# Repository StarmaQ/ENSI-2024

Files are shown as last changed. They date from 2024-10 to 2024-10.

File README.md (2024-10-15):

This repository contains info that should hopefully help others building a line follower robot.

Files for the design of 5mayes are available, and the code for it too.

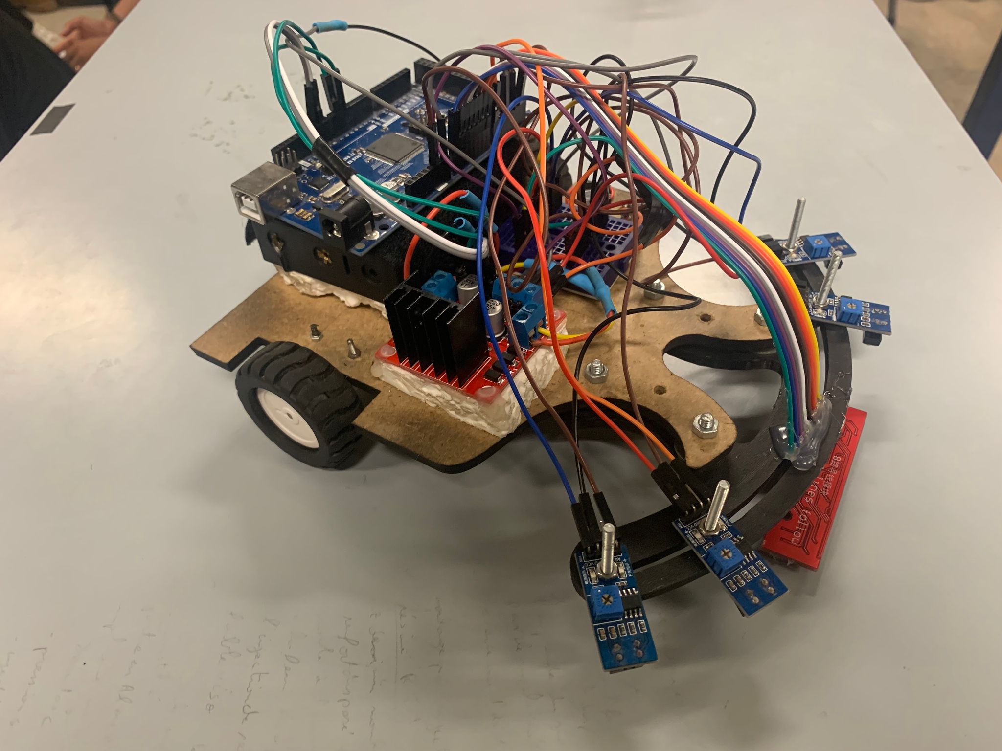
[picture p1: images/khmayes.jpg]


We used 4 IR Sensors (respectively named `farLeft`, `left`, `right` `farRight`), and the `qtr-8a`.

For generally following the line, we used the `qtr-8a`, `left` and `right` the and the PID algorithm (with $K_p = 0.06$ and $K_d = 0$).

At first our PID algorithm only relied on the `qtr_8a`, but we noticed a very good improvement when we added `left` and `right` to the error calculation, giving both very high weights compared to the middle sensors of the qtr. This made it it impossible for 5mayes to exit the line, as it strongly corrected itself if it did so.

With the PID alone we were able to traverse most of the map, but we had to flag various sections of the map, to be aware of where 5mayes was, and what the next obstacle was. 

Flagging each obstacle involved making 5mayes move, setting up a flag that involved checking what combination of `isRight()`, `isLeft()`, `isFarLeft()` and `isFarRight()` was returning true (we even relied on the values from the qtr using `digitalSensors[i]` for some flags), calling `robotStop()` when the flag was activated to debug whether the flag was correct or not, and whether it had a high chance of failure or not.

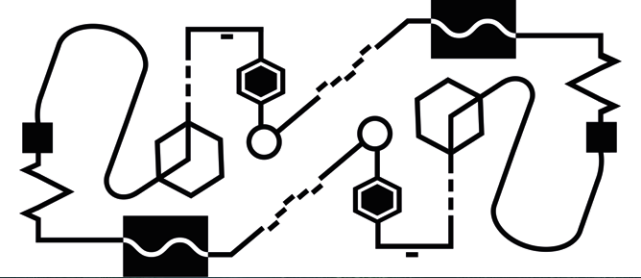
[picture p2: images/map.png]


The main thing about making a line follower robot is having consistent results no matter the conditions, and discovering what factors were at apply for it give to stable results was the difficulty of the challenge.

There were two major changes to 5mayes that were essential for us to achieve decent results, first one was hardware. We had a hard time at first with the IR sensors falling off their place, their height off the ground changing which made their values change, and as such we had to change threshhold and numbers all the time. The frontal part was original just MDF, we ended up 3D printing it making it more robust, and we made sure all the sensors were firmly fixed in place such that their heights don't change and their values would then become generally the same each time we tested.

Second most important change was adding an automatic calibrating function. We did two things here, we agreed on a good range of values that worked well with the threshholds and with the range for the error we calculated for the PID algorithm. Inside of `void setup()` we made a function to register the max and min value for each sensor, and then any value read during `void loop()` would be mapped from that min/max range to the range we want (e.g. IR sensors readings were always mapped between 0 and 700, as such our threshhold of 200 worked perfectly every time we tested).

Another addition was a formula we applied to our qtr. It was giving us really bad numbers, (600 when over white, 780 when over black), which resulted in an error that wouldn't make the PID algorithm function perfectly. Besides mapping to the range (0, 1023) which had a linear effect on the values, we had to apply a smoothing formula, that pretty much made values underneath a certain threshhold negligible, and favored higher values that were closer to 1023. This gave us perfect numbers that we were able to work with

```c
sensorValues[i] = (int)(pow((long double)sensorValues[i]/700, 12)*350);
```

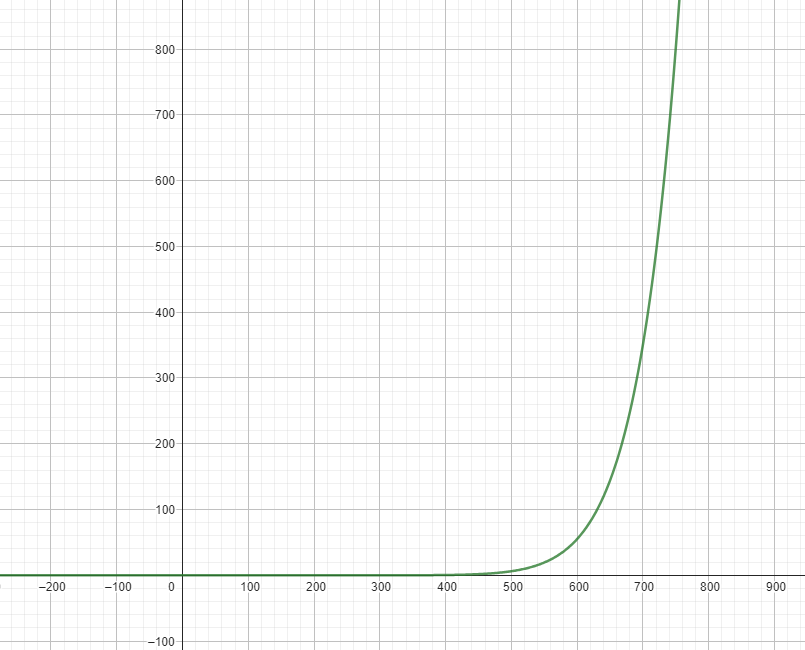
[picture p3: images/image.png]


With this, values that were under 700 were generally squashed down so that they wouldn't effect the error.

Despite our robot performing well in the map we had fil INSAT finishing most of it, it performed poorly in the ENSI, barely finishing a quarter of the map. 

Our mistake was we didn't make sure our flags were rock solid and that they worked every single time. The difficulty with line followers is having consistent results. 

Another advice is to make sure you save your latest working code! It can easily be lost, we had this issue the day of the event, and we were using code we weren't sure about, and we even made untested last minute changes that probably contributed to the 5mayes not working!

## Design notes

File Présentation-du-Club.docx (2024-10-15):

DOSSIER THECHNIQUE DU ROBOT :

KHMAYES

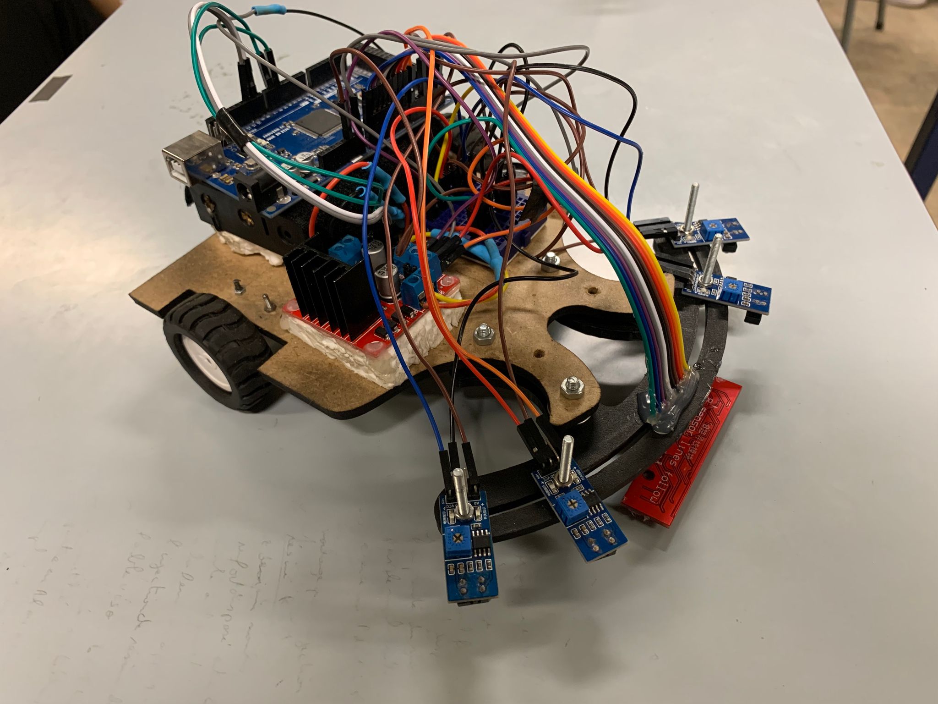
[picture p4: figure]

Présentation du Club :

Notre club est leader dans le domaine de la robotique et de l’aéronautique en Tunisie, et représente le pôle robotique et Aéronautique de l’INSAT. AEROBOTIX est une famille renfermant plus de 150 membres. Nous cherchons à rendre chaque rencontre enrichissante d’un point de vue humain et technologique. Chaque membre apporte de l’énergie aux autres, nous nous attachons à insuffler cette énergie pour innover et concrétiser nos projets qui feront objets des compétitions et des expositions nationales et internationales. Nous offrons une excellente formation pour nos membres et nous garantissons une expérience innovante, exceptionnelle et collaborative. Notre club est le club le plus performant à l’INSAT avec plus de 100 participations à des compétitions nationales, 17 participations à l’échelle internationale et remportant ainsi plusieurs prix, plus que 35 médailles et 25 trophées.

Introduction :

Le but de ce projet était de réaliser un robot capable de suivre une ligne qu’elle soit droite ou courbe. La mise en œuvre pratique était que notre robot puisse participer à une course contre le robot n˚2, réalisé par un autre groupe. La principale contrainte à laquelle nous avons dû faire face était la taille du robot, la gestion du temps et la difficulté du map. En effet, celui-ci devait respecter les dimensions mentionnées dans le cahier des charges du ROBOCUP ENSI 7.0. Pour concevoir notre robot, on nous a fourni différents éléments tels que les moteurs, les roues et la carte Arduino sur laquelle nous avons programmé le robot.

Projet

Conception sous solidworks

Realisation du cablage

Realisation du programme

Choix de la strategie

Conception du robot

Informatique

mécanique

electrique

Partie mécanique :

Pour la partie mécanique, Nous avons d’abord réfléchi sur une feuille sur laquelle nous dessinions les composants, puis on a choisi SolidWorks comme logiciel pour dimensionner notre robot en 3d. Nous avons conçu 2 bases différentes, puis nous les avons assemblés

Nous avons d’abord tracé notre base sur le bois (MDF), puis nous avons découpé celle-ci. Nous avons ensuite dû fixer un morceau de bois à angle droit sur la partie arrière il nous a juste fallu choisir les vis adaptées pour attacher les deux morceaux de bois.

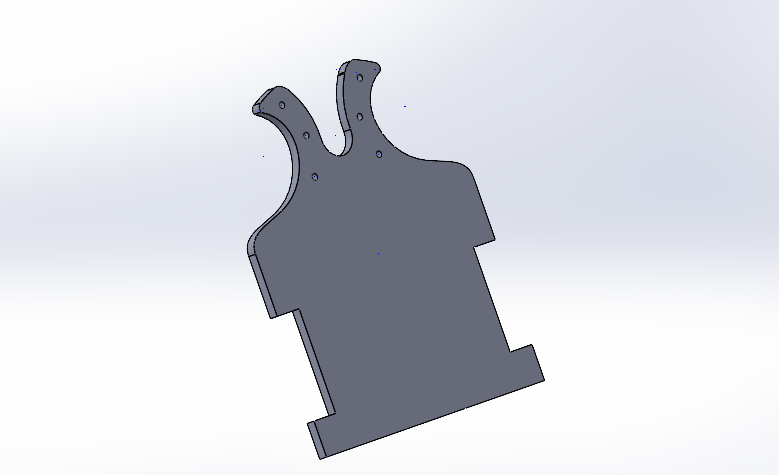
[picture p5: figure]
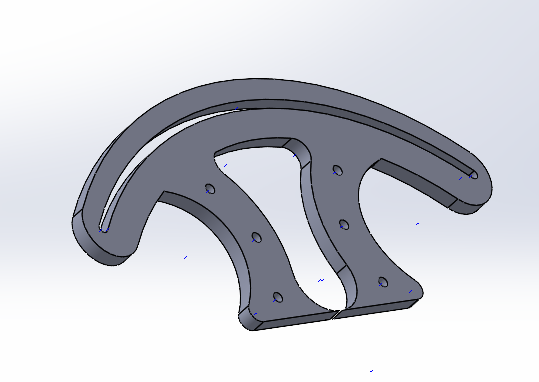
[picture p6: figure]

Composants utilisés :

QTR sensor :

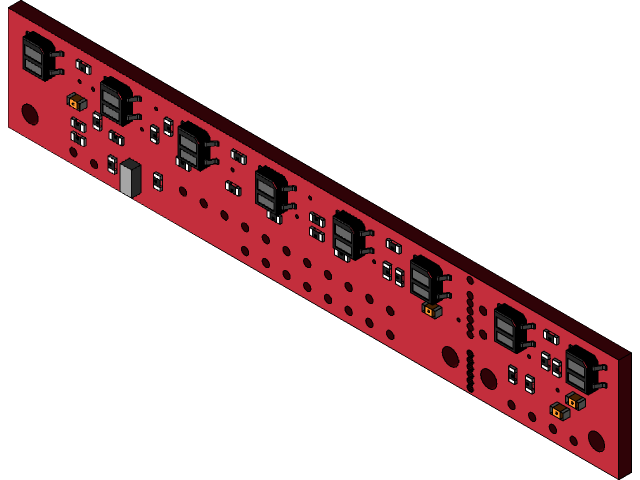
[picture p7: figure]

Moteur pololu :

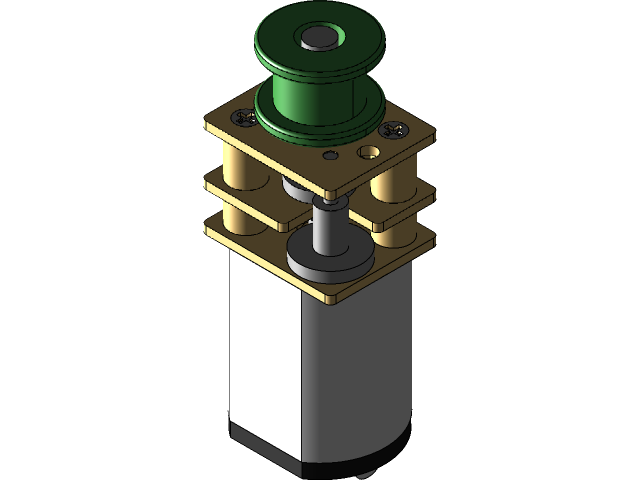
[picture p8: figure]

Carte Arduino méga :

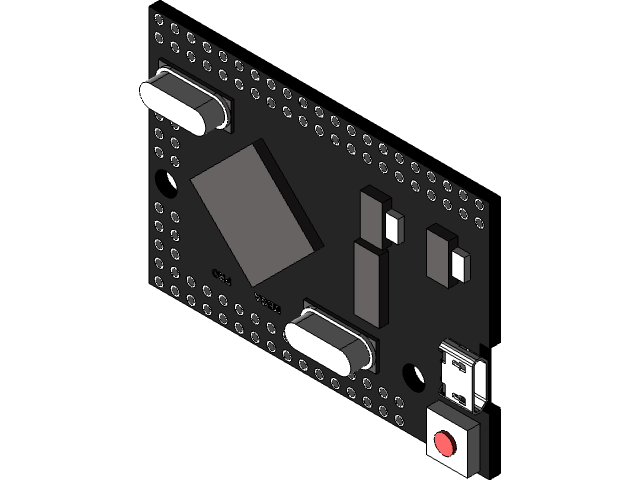
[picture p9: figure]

Capteur infrarouge :

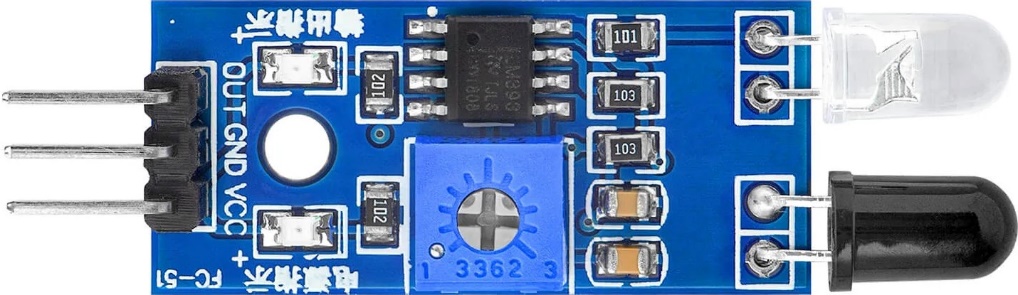
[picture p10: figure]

Carte de puissance :

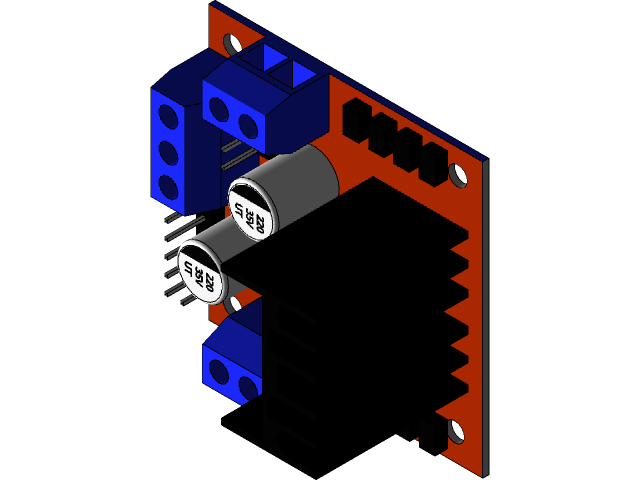
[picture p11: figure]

SCROLL

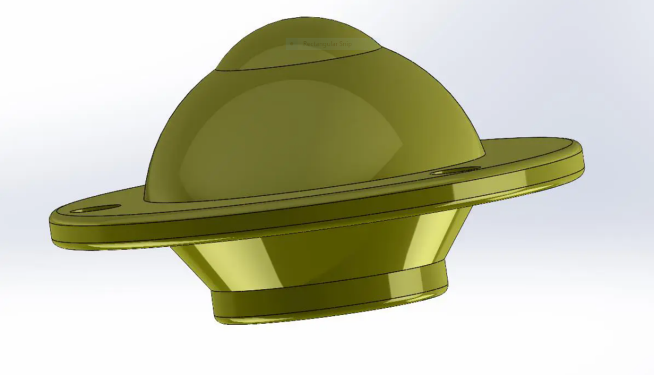
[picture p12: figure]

3 piles :

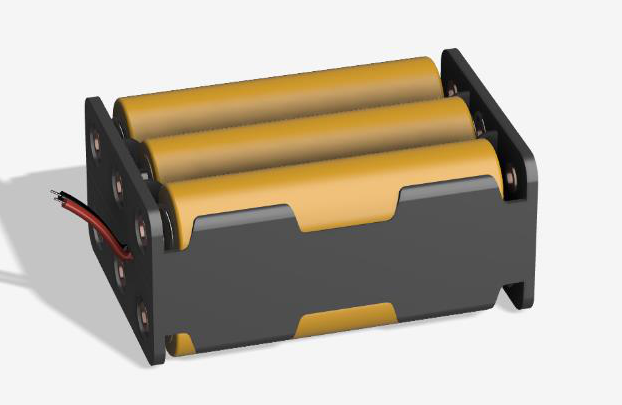
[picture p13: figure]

Conception électronique :

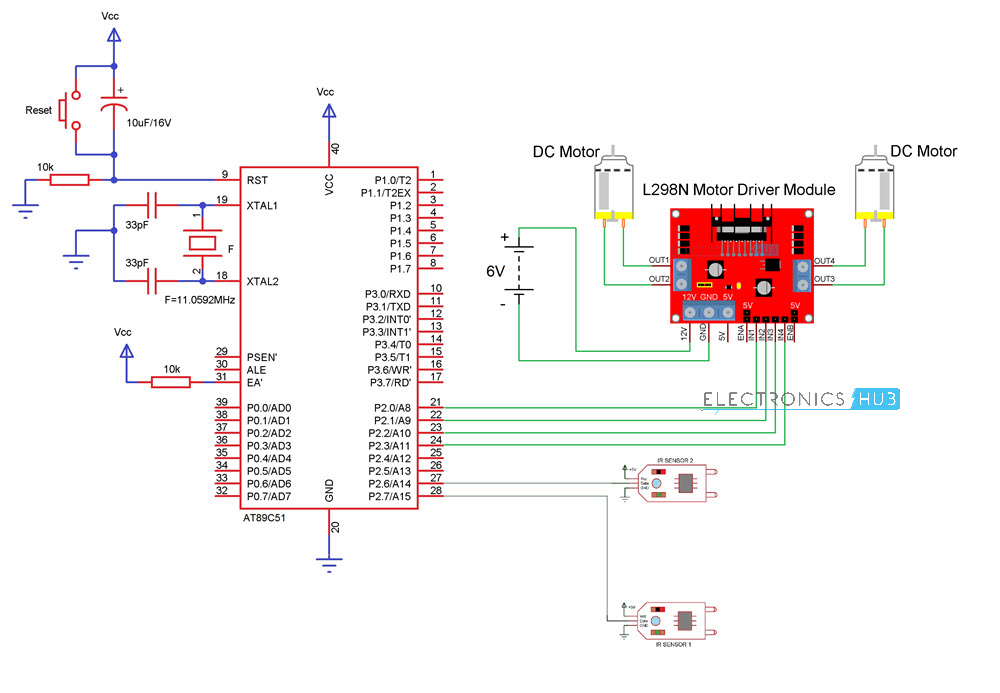
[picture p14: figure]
Line Follower Robot using Microcontroller | Engineering Projects

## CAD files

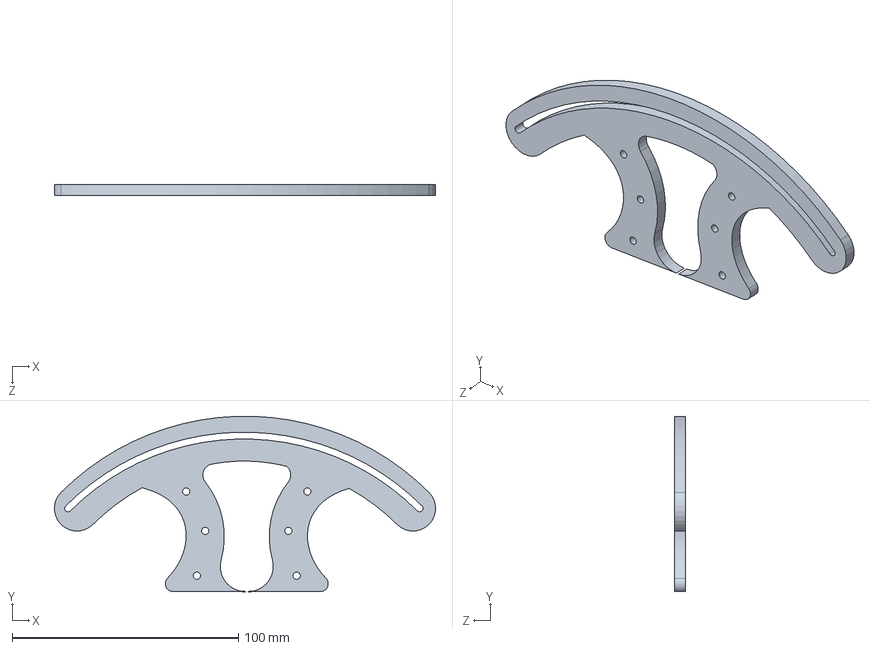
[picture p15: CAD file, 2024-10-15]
khmayess-up (1).sldprt
168.3 x 77.4 x 5.00 mm

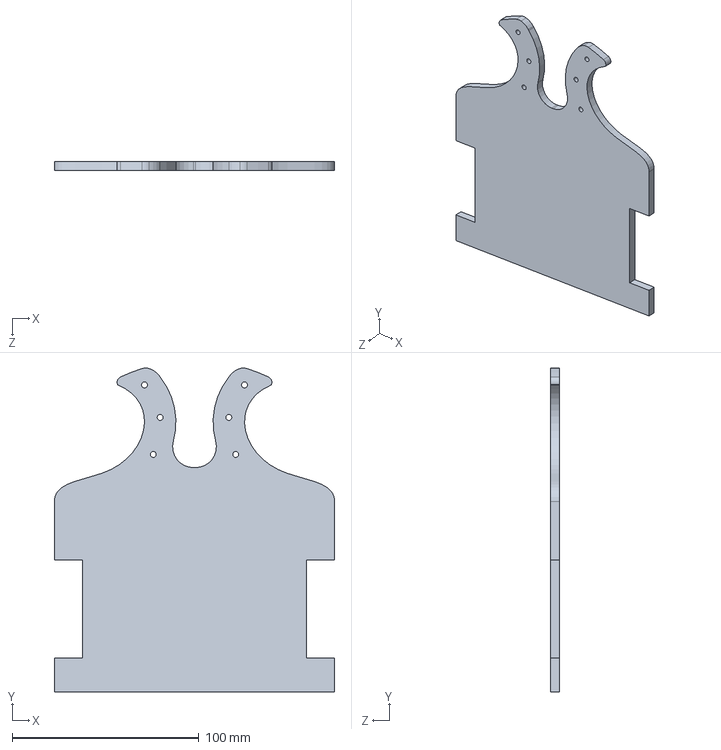
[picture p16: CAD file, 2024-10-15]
khmayessss-down (1).sldprt
150.0 x 173.4 x 5.00 mm

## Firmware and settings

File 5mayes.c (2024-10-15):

#include <QTRSensors.h>

#define m1p1 5
#define m1p2 6

#define m2p1 10
#define m2p2 9

#define rs A8
#define ls A12

#define rs2 A14
#define ls2 A11

#define NUM_SENSORS 8

float Kp = 0.06;
#define Kd 0

#define rightMaxSpeed 250
#define leftMaxSpeed 250
int cond = 0;

int inclination = 0;
int leftBaseSpeed = 120;
int rightBaseSpeed = 120;
#define threshhold 250;

QTRSensors qtra;
uint16_t sensorValues[NUM_SENSORS];
uint16_t digitalSensors[NUM_SENSORS];

#define BUFFER_SIZE 10
int rightSensorValues[BUFFER_SIZE];
int leftSensorValues[BUFFER_SIZE];
int farRightSensorValues[BUFFER_SIZE];
int farLeftSensorValues[BUFFER_SIZE];
int rightTotal = 0;
int leftTotal = 0;
int farRightTotal = 0;
int farLeftTotal = 0;
int currentIndex = 0;

bool inSecondHexagon = false;

long MAXIMUM_QTR;
long MINIMUM_QTR;


int minIRValues[4];
int maxIRValues[4];

// function to calibrate the sensors
void calibrate() {
  for (int i = 0; i < 4; i++) {
    minIRValues[i] = 1000;
    maxIRValues[i] = 0;
  }

  // for (int i = 0; i < 100; i++) {  // 100 iterations of calibration
  while (digitalRead(3) == 1) {
    int leftSensor = analogRead(ls);
    int rightSensor = analogRead(rs);
    int leftSensor2 = analogRead(ls2);
    int rightSensor2 = analogRead(rs2);

    // Update minimum values
    if (leftSensor < minIRValues[0]) minIRValues[0] = leftSensor;
    if (rightSensor < minIRValues[1]) minIRValues[1] = rightSensor;
    if (leftSensor2 < minIRValues[2]) minIRValues[2] = leftSensor2;
    if (rightSensor2 < minIRValues[3]) minIRValues[3] = rightSensor2;

    // Update maximum values
    if (leftSensor > maxIRValues[0]) maxIRValues[0] = leftSensor;
    if (rightSensor > maxIRValues[1]) maxIRValues[1] = rightSensor;
    if (leftSensor2 > maxIRValues[2]) maxIRValues[2] = leftSensor2;
    if (rightSensor2 > maxIRValues[3]) maxIRValues[3] = rightSensor2;

    // function provided by the qtra library
    qtra.calibrate();
  
    delay(10);
  }


  long sumMaximum = 0;
  long sumMinimum = 0;

  for (int i = 0; i < NUM_SENSORS; i++) {
    sumMaximum = sumMaximum + qtra.calibrationOn.maximum[i];
    sumMinimum = sumMinimum+ qtra.calibrationOn.minimum[i];
  }
  MAXIMUM_QTR=sumMaximum/(NUM_SENSORS);
  MINIMUM_QTR=sumMinimum/(NUM_SENSORS);
}

void setup() {
  pinMode(m1p1, OUTPUT);
  pinMode(m1p2, OUTPUT);
  pinMode(m2p1, OUTPUT);
  pinMode(m2p2, OUTPUT);
  pinMode(LED_BUILTIN, OUTPUT);
  pinMode(3, INPUT_PULLUP);
  qtra.setTypeAnalog();
  qtra.setSensorPins((const uint8_t[]){A0, A1, A2, A3, A4, A5, A6, A7}, NUM_SENSORS);

  Serial.begin(9600);

  // Serial.println("calibrating");
  calibrate();
  // Serial.println("Done calibratin");

  for (int i = 0; i < BUFFER_SIZE; i++) {
    rightSensorValues[i] = 0;
    leftSensorValues[i] = 0;
  }

  delay(2000);

  mforward(100);
  delay(500);
}

void readQtr() {
  qtra.read(sensorValues); 

  for (unsigned char i = 0; i < NUM_SENSORS; i++)
  {

    sensorValues[i] = map((long)sensorValues[i], MINIMUM_QTR, MAXIMUM_QTR, 580, 760);

    sensorValues[i] = (int)(pow((long double)sensorValues[i]/700, 12)*350);
    //   Serial.print(sensorValues[i]);
    // Serial.print("\t");
    digitalSensors[i] = (sensorValues[i] > 700) ? 1 : 0;
    //    Serial.print(digitalSensors[i]);
    // Serial.print("\t");
  }

  // Serial.println();
}

int right;
int left;
int farRight;
int farLeft;
int rightWeight = -8000;
int leftWeight = 8000;

void readIR() {
    left = map(constrain(analogRead(ls), minIRValues[0], maxIRValues[0]), minIRValues[0], maxIRValues[0], 30, 750);
    right = map(constrain(analogRead(rs), minIRValues[1], maxIRValues[1]), minIRValues[1], maxIRValues[1], 30, 750);
    farLeft = map(constrain(analogRead(ls2), minIRValues[2], maxIRValues[2]), minIRValues[2], maxIRValues[2], 30, 750);
    farRight = map(constrain(analogRead(rs2), minIRValues[3], maxIRValues[3]), minIRValues[3], maxIRValues[3], 30, 750);

    // Serial.print(farLeft);
    // Serial.print("\t");
    //  Serial.print(left);
    // Serial.print("\t");
    //  Serial.print(right);
    // Serial.print("\t");
    //  Serial.print(farRight);
    // Serial.println("\t");
}

int entryTime = 0;
int sharpTurnsActivated = 0;
bool firstSharpTurn = 0;

void loop() {
    
    readQtr(); 
    readIR();

    // filterStep();


    if (cond == 0 && isFarLeft()) { // enter hexagon
        cond = 1;
        sharpRight(250);
        while (isFarLeft() || isLeft() || isFarRight()) {
            readIR();
            readQtr();
        }
        entryTime = millis();
    } 
    
    if (cond == 1 && isFarLeft() && (millis() - entryTime) > 1500) { // leave hexagon
        cond = 2;
        sharpRightOneWheel(100);
        while (isLeft()) {
            readIR();
        }
        
        entryTime = millis();
    }

    if (cond == 2 && (isRight()) && (millis() - entryTime) > 1500) { // first sharp turn
        cond = 3;
        sharpRight(250);
        entryTime = millis();
    }

    // right or left pad, it can be any of the randomly

    if (cond == 3 && (isRight() || isLeft() || isFarRight() || isFarLeft()) && (millis() - entryTime) > 500) {
        cond = 4;


        entryTime = millis();
    }

    // second sharp turn, we apply custom logic here so that 5mayes turns perfectly to line with the hexagon
    if (cond == 4 && (isRight() || isFarRight()) && (millis() - entryTime) > 350) {
        cond = 5;
        entryTime = millis();
        mforward(60);
        rightWeight = 0;
        leftWeight = 0;
        // move forward until none of the sensors are on the line
        while (isRight() || isFarRight() || isLeft() || isFarLeft()) {
            readIR();
            readQtr();
        }
        delay(400);
    
        sharpRight(60);

        // turn until aligned with the line
        while (!digitalSensors[3] || !digitalSensors[4]) {
            readQtr();
        }

        rightBaseSpeed = 40;
        leftBaseSpeed = 40;
        mforward(100);
        
        // move until before entering the hexagon
        while (!isRight() && !isLeft()) {
           readIR();
        }

    }

    if (cond == 5) {
        cond = 6;

        mforward(160);

        delay(500);
        
        stopRobot();
        delay(2000);  // 5000
        rightWeight = -50000;
        leftWeight = 8000;
        mforward(100);
        delay(350); // 350
        readQtr();
        entryTime = millis();
    }

    // enter rond point
    if (cond == 6 && isLeft() && (millis() - entryTime) > 750) {
        cond = 7;
        entryTime = millis();
        sharpLeft(200);
    }

    // leave rond point
    if (cond == 7 && isLeft() && (millis() - entryTime) > 500) {
        delay(150);
        sharpLeft(200);
        while (!isFarRight()) {readIR();}
        cond = 8;
        rightWeight = -8000;
        leftWeight = 8000;

        // making the robot faster made the enter white flag function more often
        rightBaseSpeed = 200;
        leftBaseSpeed = 200;  
    }

    // enter white path, we invert the logic here
    if (cond == 8 && ((isFarRight() || isFarLeft()) && (!digitalSensors[3] || !digitalSensors[4]))) {
        entryTime = millis();
        rightWeight = 0;
        leftWeight = 0;
        rightBaseSpeed = 60;
        leftBaseSpeed = 60;
        while (!digitalSensors[3] && !digitalSensors[4] && ((millis() - entryTime) > 1000 ? (isFarLeft() || isFarRight()) : true)) {// while (!digitalSensors[3] && !digitalSensors[4] && (!isRight() || !isLeft() || !isFarLeft() || isFarRight())) {
        readQtr();
        readIR();

        for (int i = 0; i < NUM_SENSORS; i++) {
            sensorValues[i] = constrain(1023-sensorValues[i], 0, 1023);
        }

        PID();
        delay(25);
        }
        
        rightBaseSpeed = 120;
        leftBaseSpeed = 120;
        rightWeight = -8000;
        leftWeight = 8000;
        cond = 9;

        if (!isFarLeft()) {
            while (!isFarLeft()) {
                readIR();
                sharpLeft(60);
            }
            } else {
            while(!isFarRight()) {
                readIR();
                sharpRight(60);
            }
        }
    
        
        entryTime = millis();
    }

    // same logic as second sharp turn
    if (cond == 9 && (isRight() || isFarRight()) && (millis() - entryTime) > 350) {
        cond = 10;
        entryTime = millis();
        mforward(60);
        rightWeight = 0;
        leftWeight = 0;
        while (isRight() || isFarRight() || isLeft() || isFarLeft()) {
            readIR();
            readQtr();
        }
        delay(400);

        sharpRight(60);

        while (!digitalSensors[3] || !digitalSensors[4]) {
            readQtr();
        }
    }

    // zig zag, we just do hardcoded trash code here
    if (cond == 10 && isFarLeft()) {
        cond = 11;
        sharpLeft(40);

        while (isLeft() || isFarLeft()) {
            readIR();
        }

        mforward(40);

        while (!isWhite() || isRight() || isLeft() || isFarLeft() || isFarRight()) {
            readIR();
            readQtr();
        }

        sharpRight(40);

        while (!(digitalSensors[3] && digitalSensors[4])) {
            readQtr();
        }

        while (!isWhite() || isRight() || isLeft() || isFarLeft() || isFarRight()) {
            readIR();
            readQtr();
            PID();
        }

        sharpLeft(40);

        while (!(digitalSensors[3] && digitalSensors[4])) {
            readQtr();
        }

        while (!isWhite() || isRight() || isLeft() || isFarLeft() || isFarRight()) {
            readIR();
            readQtr();
            PID();
        }

        sharpLeft(40);

        while (isLeft() || isFarLeft()) {
            readIR();
        }

        sharpRight(40);

        while (!(!isLeft() && !isRight() && !isFarRight() && !isFarLeft() && digitalSensors[5] && digitalSensors[6] && digitalSensors[7] && !digitalSensors[0] && !digitalSensors[1] && !digitalSensors[2] && !digitalSensors[3] && !digitalSensors[4])) {
            readIR();
            readQtr();
        }

        readQtr();

        while (!(isFarLeft() && isLeft())) {
            readIR();
            readQtr();
            PID();
        }


        sharpLeft(40);

        while (!(isFarRight())) {
            readIR();
        }

        mforward(100);
        delay(800);

        stopRobot();
        while (1) {}
    }

    PID();

  delay(10);
}

// error caulcating function
// every sensor is assigned a weight, the more to the right it is the more negative
int calculateLinePosition(unsigned int *sensorValues, uint8_t sensorCount) {
    float weightedSum = 0;
    float totalValue = 0;
    
    for (int i = 0; i < sensorCount; i++) {
        float weight = (i - 3.5) * 1000; 
        weightedSum += sensorValues[i] * weight;
        totalValue += sensorValues[i];
    }

    weightedSum += map(right, minIRValues[1], maxIRValues[1], 0, 1023) * rightWeight;
    totalValue += map(right, minIRValues[1], maxIRValues[1], 0, 1023);
    weightedSum += map(left, minIRValues[0], maxIRValues[0], 0, 1023) * leftWeight;
    totalValue += map(left, minIRValues[0], maxIRValues[0], 0, 1023);

    if (totalValue == 0) {
        return 0;
    }

    int position = weightedSum / totalValue;

    return position;
}

int lastError = 0;

// PID algorithm
void PID() {
    float position = calculateLinePosition(sensorValues, NUM_SENSORS) - inclination;
    
    float error = position;
    float diff = error-lastError;
  
    int motorSpeed = Kp * error + Kd * diff; // PID formula
    // edit motor speeds depending on the error, add for right motor, subtract for left, as such the robot turns
    int rightMotorSpeed = rightBaseSpeed + motorSpeed;
    int leftMotorSpeed = leftBaseSpeed - motorSpeed;

    
    rightMotorSpeed = constrain(rightMotorSpeed, 0, rightMaxSpeed);
    leftMotorSpeed = constrain(leftMotorSpeed, 0, leftMaxSpeed);

    analogWrite(m1p1, rightMotorSpeed);
    analogWrite(m1p2, 0);
    analogWrite(m2p1, leftMotorSpeed);
    analogWrite(m2p2, 0);
}

bool isRight() {
     return right >= threshhold;
}

bool isLeft() {
    return left >= threshhold;
}

bool eitherRight() {
    return isRight() || isFarRight();
}

bool eitherLeft() {
     return isLeft() || isFarRight();
}

bool leftAndRight() {
    return isLeft() && isRight();
}

bool isFarLeft() {
    return farLeft >= threshhold;
}

bool isFarRight() {
    return farRight >= threshhold;
}

// if most of the front sensors are white, then in front is white, used for some flags

int weights[NUM_SENSORS] = {1, 3, 4, 4, 3, 1};

bool isWhite() {
    int weightedSum = 0;
    int weightTotal = 0;

    for (int i = 0; i < NUM_SENSORS; i++) {
        weightedSum += sensorValues[i] * weights[i];
        weightTotal += weights[i];
    }

    // Calculate weighted average
    int weightedAverage = weightedSum / weightTotal;

 
    if (weightedAverage < 250) {
        return true;  // White detected
    } else {
        return false;  // Black detected
    }
}


void sharpRight(int speed) {
    analogWrite(m1p1, 0);
    analogWrite(m1p2, speed);
    analogWrite(m2p1, speed);
    analogWrite(m2p2, 0);
}

void sharpRightOneWheel(int speed) {
    analogWrite(m1p1, 0);
    analogWrite(m1p2, 0);
    analogWrite(m2p1, speed);
    analogWrite(m2p2, 0);
}

void sharpLeft(int speed) {
    analogWrite(m1p1, speed);
    analogWrite(m1p2, 0);
    analogWrite(m2p1, 0);
    analogWrite(m2p2, speed);
}

void stopRobot() {
    analogWrite(m1p1, 0);
    analogWrite(m1p2, 0);
    analogWrite(m2p1, 0);
    analogWrite(m2p2, 0);
}
void mforward(int speed){
    analogWrite(m1p1, speed);
    analogWrite(m1p2, 0);
    analogWrite(m2p1, speed*0.95); // 5ater moteur ysar a9wa mil limin
    analogWrite(m2p2, 0);
}

// unused function, creates a delay for sensor values
void filterStep() {
    for (int i = 0; i < BUFFER_SIZE; i++) {
        int rightSensorValue = right;
        rightTotal = rightTotal - rightSensorValues[currentIndex];
        rightSensorValues[currentIndex] = rightSensorValue;
        rightTotal = rightTotal + rightSensorValue;

        int leftSensorValue = left;
        leftTotal = leftTotal - leftSensorValues[currentIndex];
        leftSensorValues[currentIndex] = leftSensorValue;
        leftTotal = leftTotal + leftSensorValue;

        int farRightSensorValue = farRight;
        farRightTotal = farRightTotal - farRightSensorValues[currentIndex];
        farRightSensorValues[currentIndex] = farRightSensorValue;
        farRightTotal = farRightTotal + farRightSensorValue;

        int farLeftSensorValue = farLeft;
        farLeftTotal = farLeftTotal - farLeftSensorValues[currentIndex];
        farLeftSensorValues[currentIndex] = farLeftSensorValue;
        farLeftTotal = farLeftTotal + farLeftSensorValue;
    }

    currentIndex = (currentIndex + 1) % BUFFER_SIZE;
    float leftAverage = (float)leftTotal / BUFFER_SIZE;
    left = leftAverage;
    float rightAverage = (float)rightTotal / BUFFER_SIZE;
    right = rightAverage;
    float farLeftAverage = (float)farLeftTotal / BUFFER_SIZE;
    farLeft = farLeftAverage;
    float farRightAverage = (float)farRightTotal / BUFFER_SIZE;
    farRight = farRightAverage;

}
